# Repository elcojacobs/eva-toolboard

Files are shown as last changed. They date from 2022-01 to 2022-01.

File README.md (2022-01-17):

# Nema 14/17 Toolboard for EVA

Breakout board for EVA to mount to the back of a Nema 17 or name 17 motor. (31mm hole spacing or 43.8mm diagonally).

All signals and power are routed over 2 20p ribbon cables.
For the heater, 5 parallel wires are used to provide enough current. For part fan power, 2 parallel wires are used.

The same board is mounted at the hotend and near the main board.
On the main board side, most components are not mounted, only the connectors.
On the hotend side, all components are mounted except the terminal block in the middle.

## Features
- Everything wired through 2 ribbon cables.
- Spring terminal blocks for: heater, part fan, tool fan, probe, neopixel, aux 1-3
- ADXL345 on board
- Chamber temp PT1000 on board
- Neopixel LED on board and daisy chained to output terminal block
- 3 unused AUX signals

## Jumpers
- On the hotend side, connect 1 of the solder jumpers to select the voltage for the probe
- For correct neopixel routing, connect the hotend solder jumpers on the hotend side and the board solder jumpers on the main board side.

## License
Shield: [][cc-by-nc-sa]

This work is licensed under a
[Creative Commons Attribution-NonCommercial-ShareAlike 4.0 International License][cc-by-nc-sa].

[][cc-by-nc-sa]

[cc-by-nc-sa]: http://creativecommons.org/licenses/by-nc-sa/4.0/
[cc-by-nc-sa-image]: https://licensebuttons.net/l/by-nc-sa/4.0/88x31.png
[cc-by-nc-sa-shield]: https://img.shields.io/badge/License-CC%20BY--NC--SA%204.0-lightgrey.svg

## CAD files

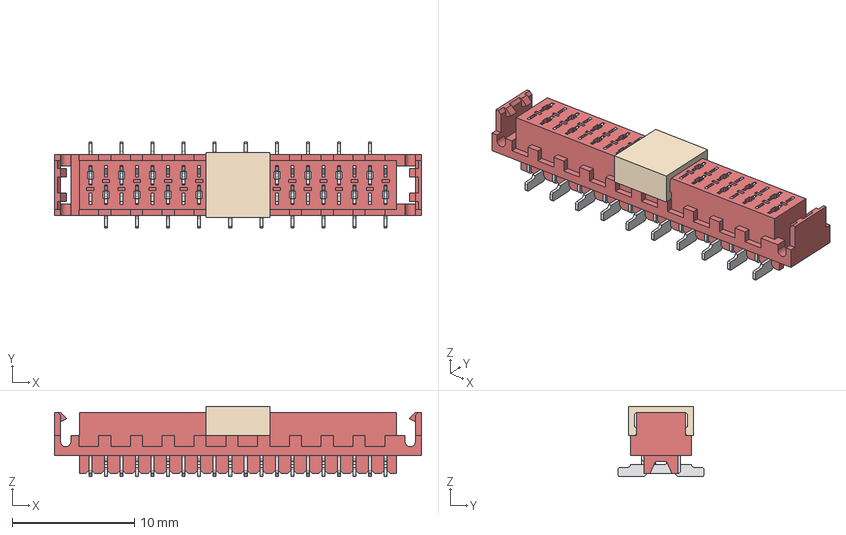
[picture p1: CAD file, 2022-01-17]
690367292076 (rev1).stp
30.0 x 7.00 x 5.75 mm
Gehäuse
Pick Pad
Pin x 20

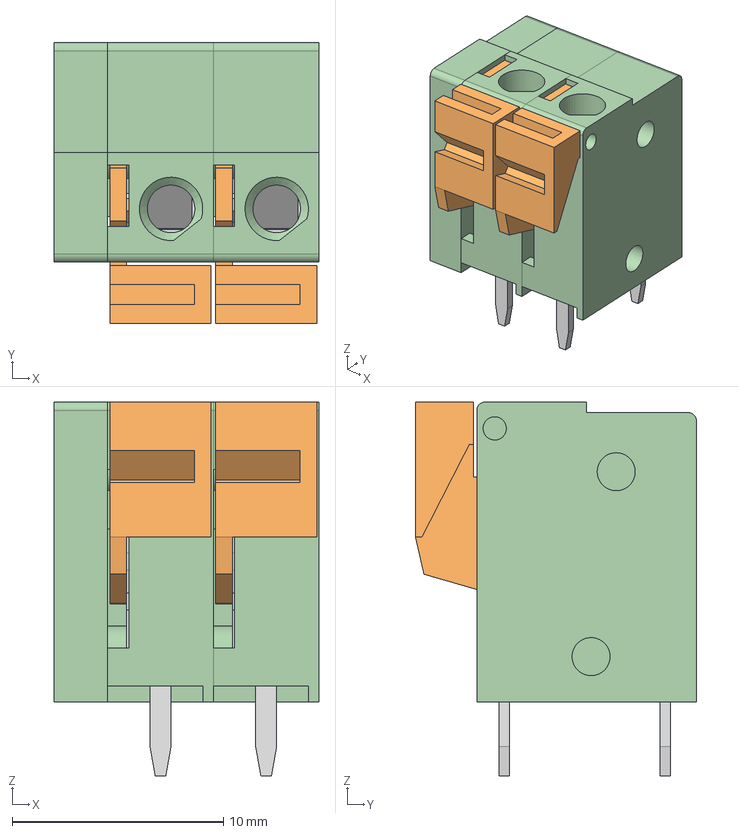
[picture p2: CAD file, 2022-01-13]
691401700002B (rev1).stp
12.5 x 13.3 x 17.7 mm
6914017000xx_CAPOT
6914017000xx x 4
6914017000xx_lame x 2
6914017000xx_Levier x 2

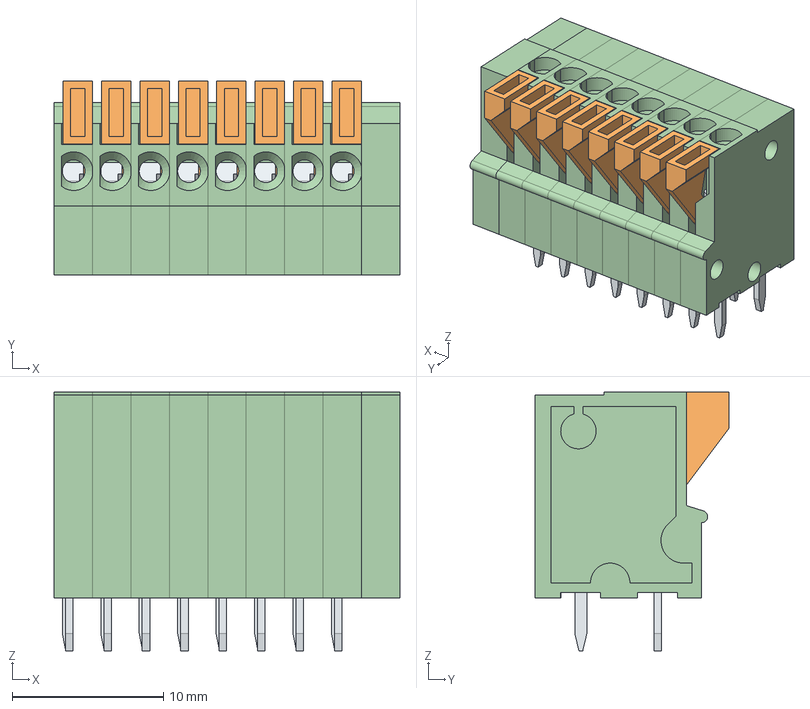
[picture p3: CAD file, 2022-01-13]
691403900008B (rev1).stp
22.9 x 12.8 x 17.1 mm
6914039000xx_CAPOT
6914039000xx x 8
6914039000xx_PIN x 8
6914039000xx_LEVIER x 8
6914039000xx_LAME x 8

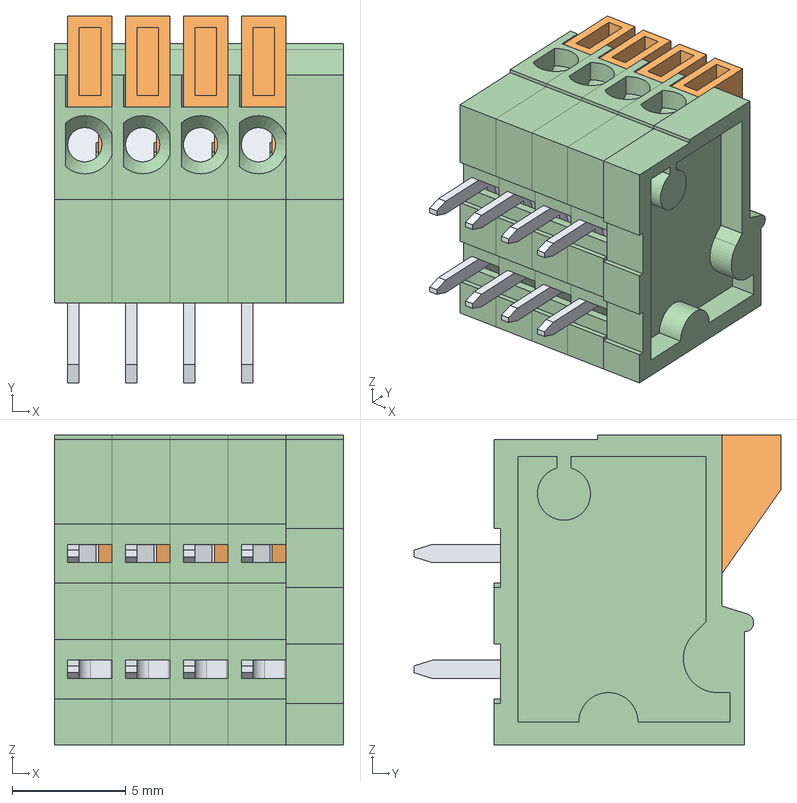
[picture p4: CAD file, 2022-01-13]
691402910004B (rev1).stp
12.7 x 16.1 x 13.6 mm
6914029100xx_CAPOT
6914029100xx x 4
6914029100xx_PIN x 4
6914029100xx_LAME x 4
6914029100xx_LEVIER x 4

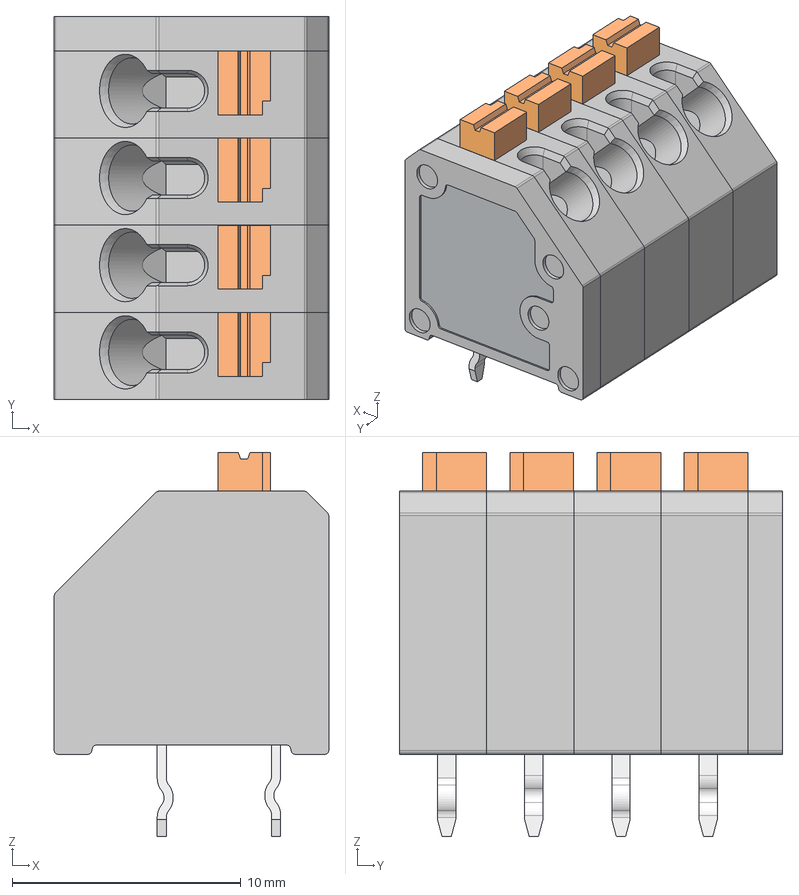
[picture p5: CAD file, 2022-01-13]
691412320004 (rev1).stp
12.0 x 16.7 x 16.8 mm
MRT24P3.81V01_SX1
MRT24P3.81V01_CNT5 x 2
MRT24P3.81V01_CNT4 x 2

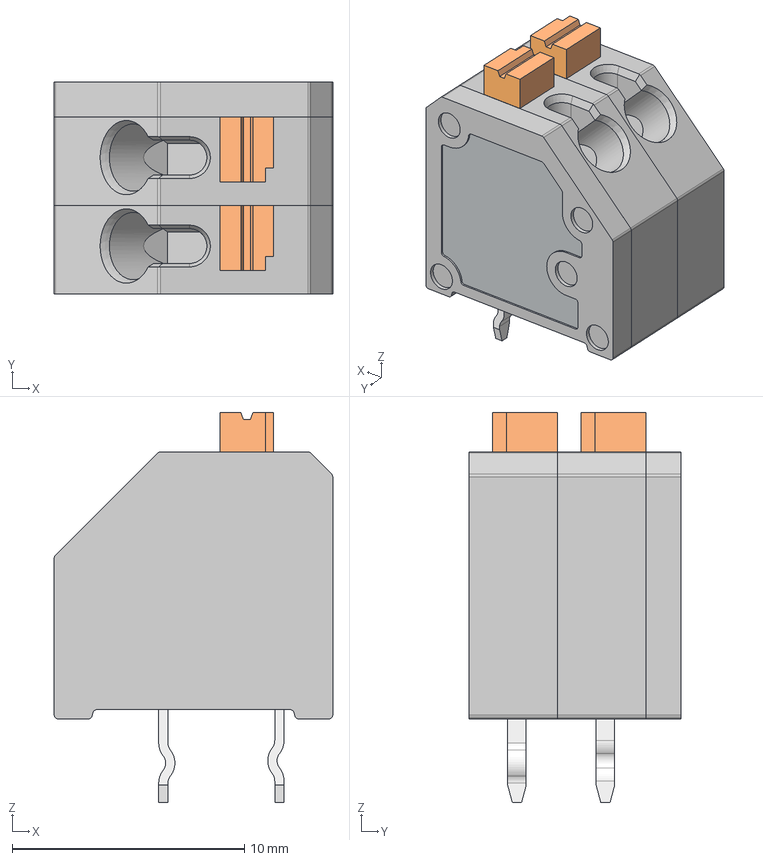
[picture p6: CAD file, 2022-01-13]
691412320002 (rev1).stp
12.0 x 9.12 x 16.8 mm
MRT24P3.81V01_SX1
MRT24P3.81V01_CNT5
MRT24P3.81V01_CNT4

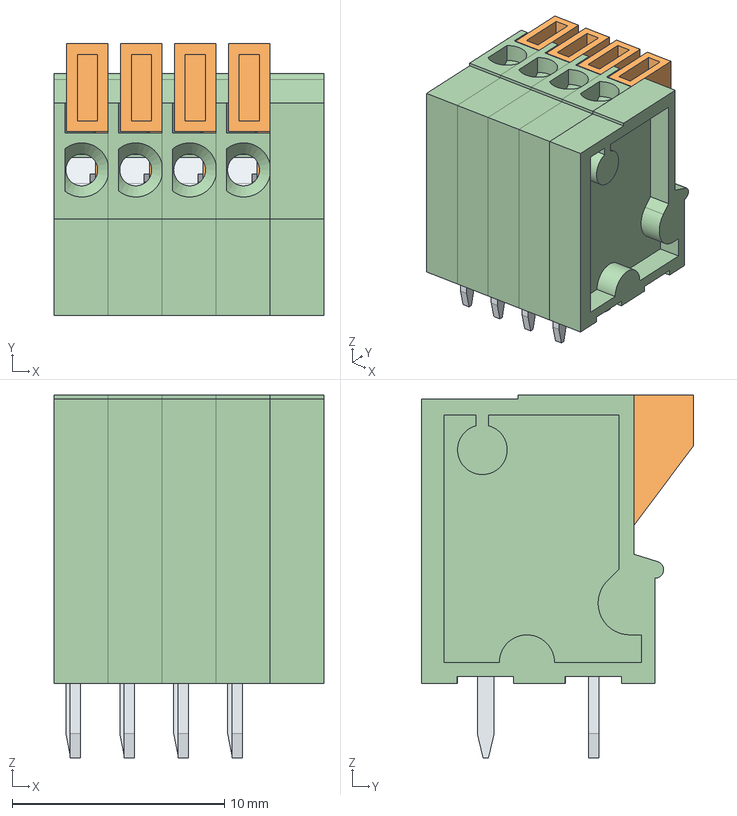
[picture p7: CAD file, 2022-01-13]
691403900004B (rev1).stp
12.7 x 12.8 x 17.1 mm
6914039000xx_CAPOT
6914039000xx x 4
6914039000xx_PIN x 4
6914039000xx_LEVIER x 4
6914039000xx_LAME x 4

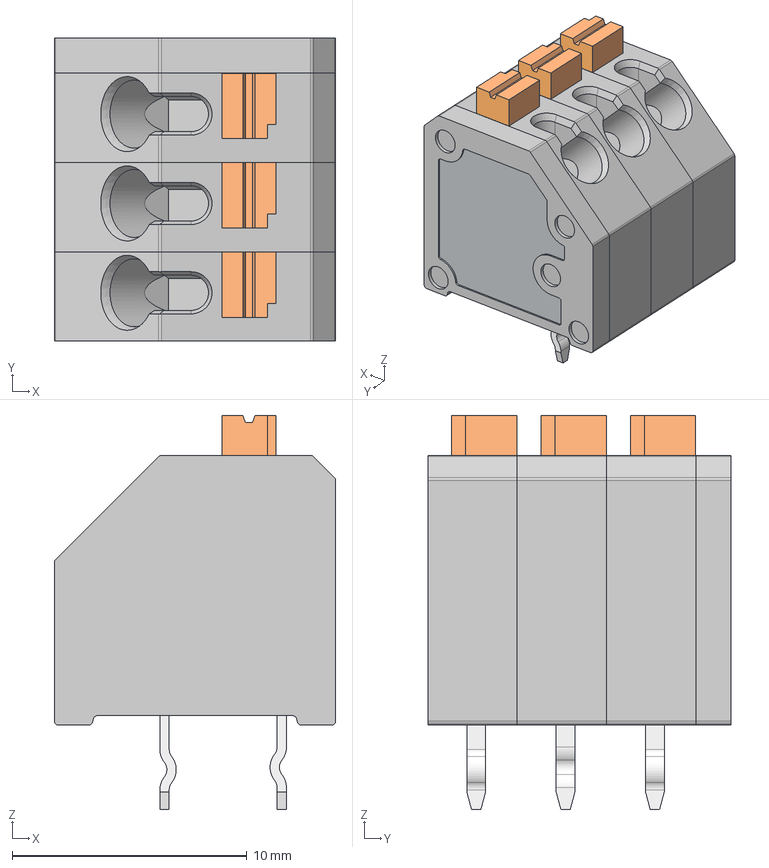
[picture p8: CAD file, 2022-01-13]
691412320003 (rev1).stp
12.0 x 12.9 x 16.8 mm
MRT24P3.81V01_SX1
MRT24P3.81V01_CNT5
MRT24P3.81V01_CNT4 x 2

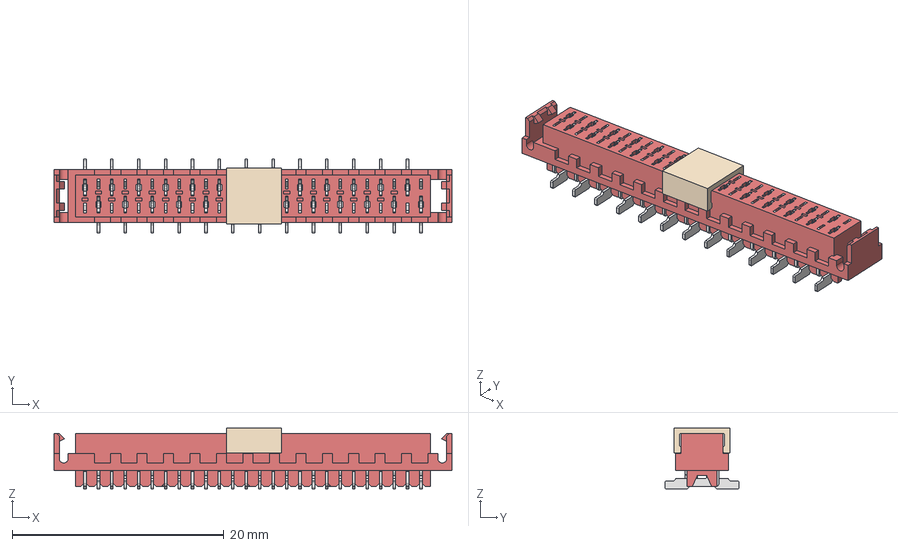
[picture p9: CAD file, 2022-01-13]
690367292676 (rev1).stp
37.6 x 7.00 x 5.75 mm
Gehäuse
Pick Pad
Pin x 26

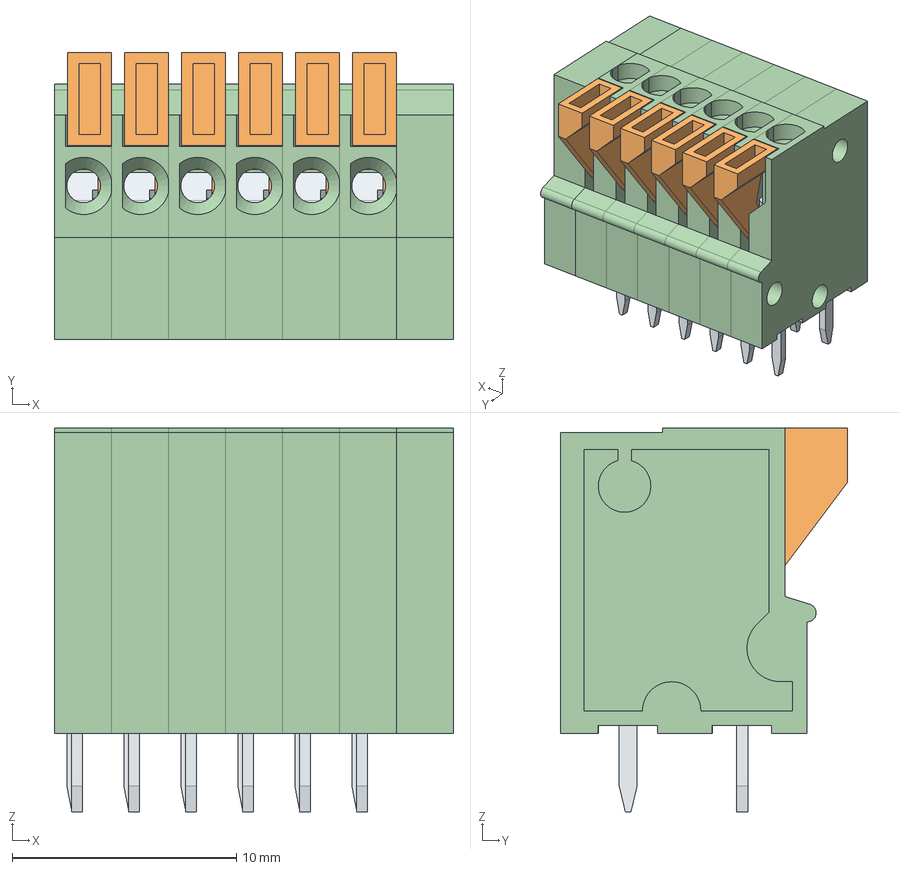
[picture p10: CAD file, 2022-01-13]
691403900006B (rev1).stp
17.8 x 12.8 x 17.1 mm
6914039000xx_CAPOT
6914039000xx x 6
6914039000xx_PIN x 6
6914039000xx_LEVIER x 6
6914039000xx_LAME x 6

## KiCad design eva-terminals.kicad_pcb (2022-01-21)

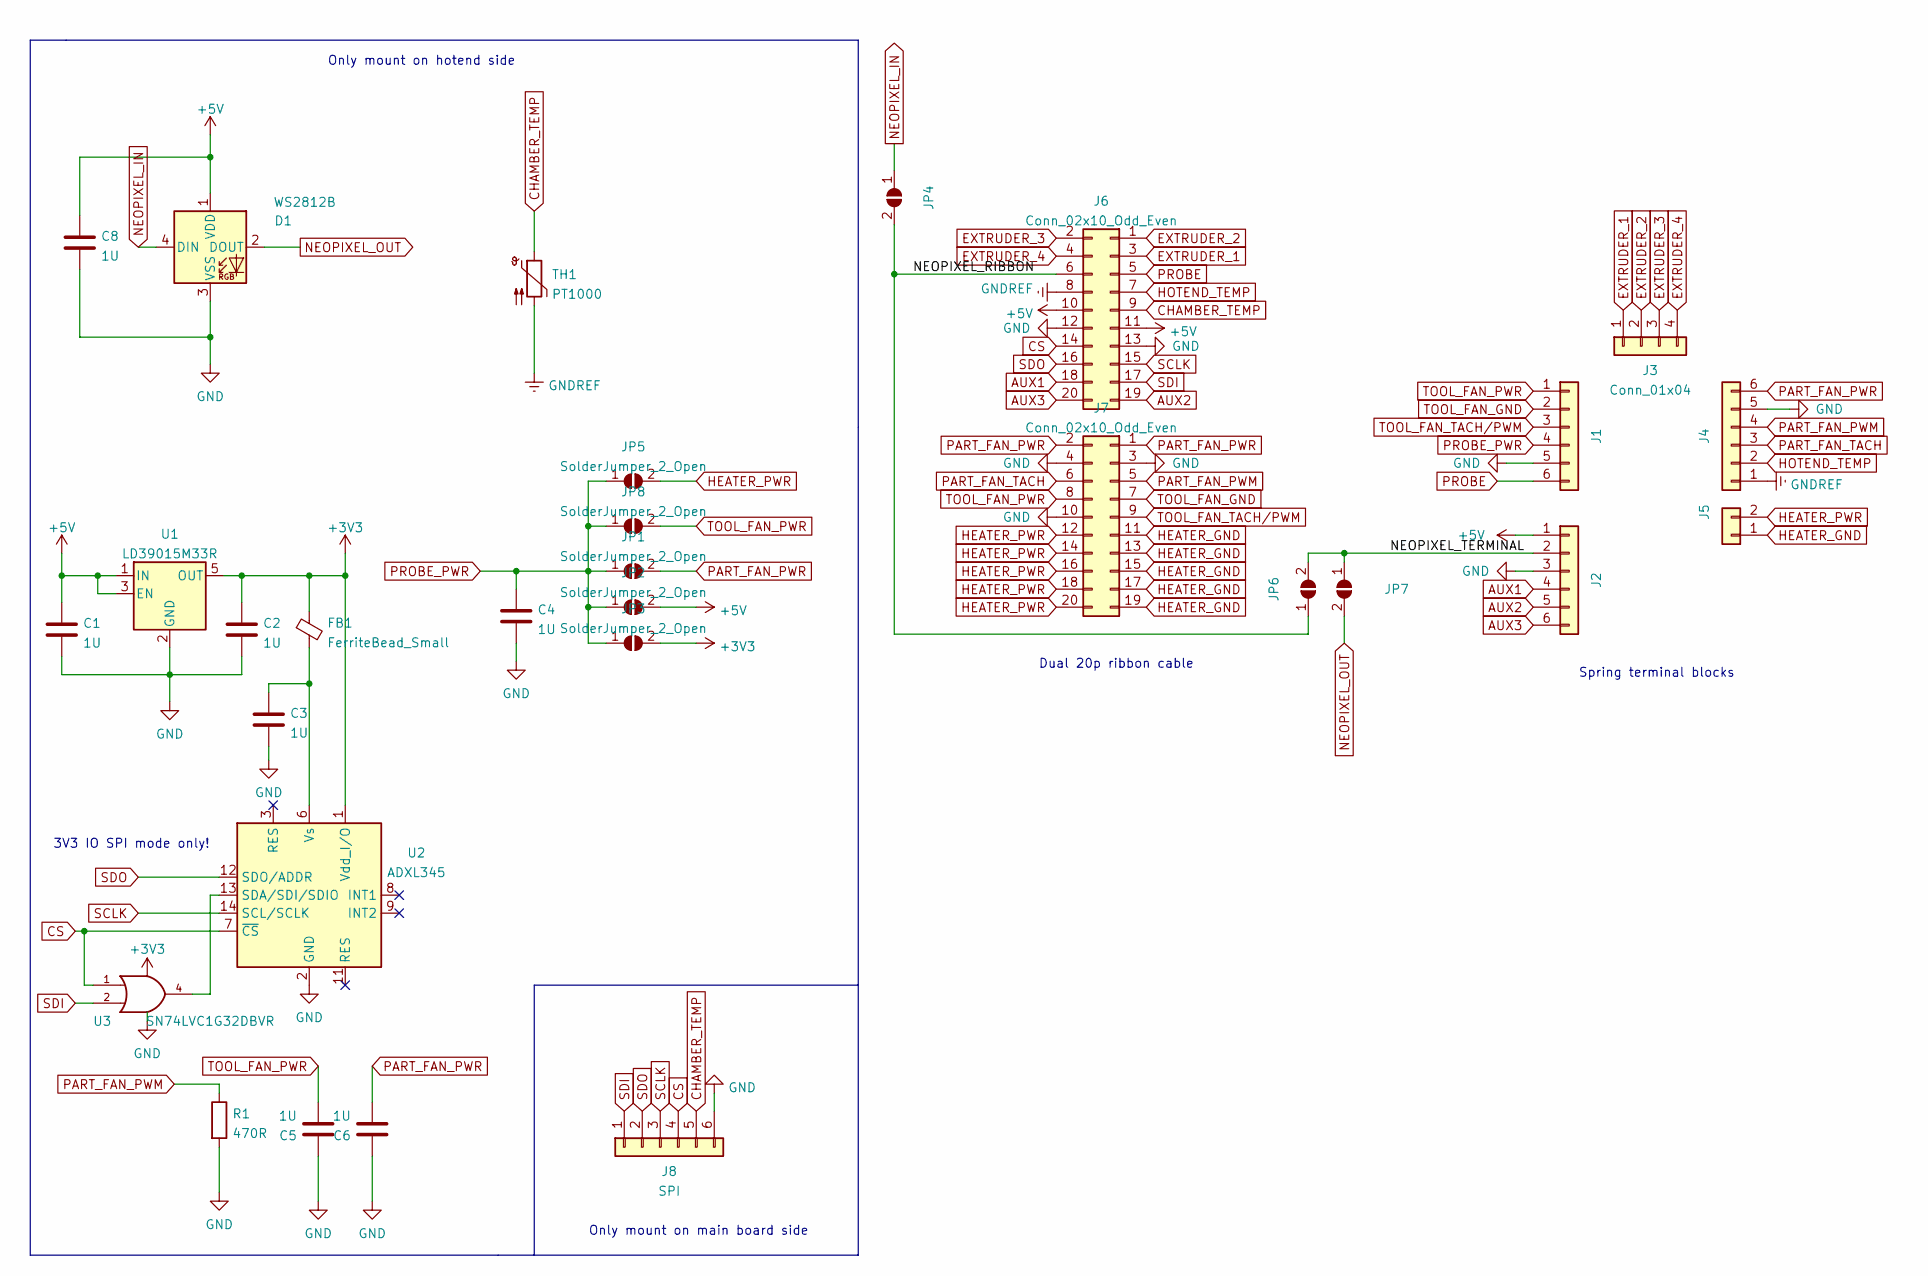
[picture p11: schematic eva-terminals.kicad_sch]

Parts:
C1, C2, C3, C4, C5, C6, C8: 1U; C_0805_2012Metric
D1: WS2812B; LED_WS2812B_PLCC4_5.0x5.0mm_P3.2mm
FB1: FerriteBead_Small; L_0603_1608Metric
J1, J2, J4: 691403900006B
J3: Conn_01x04; JST_XH_S4B-XH-A_1x04_P2.50mm_Horizontal
J5: HEATER; 691401700002B
J6, J7: Conn_02x10_Odd_Even; 690367292076
J8: SPI; 691403900006B
JP1, JP2, JP3, JP4, JP5, JP6, JP7, JP8: SolderJumper_2_Open; SolderJumper-2_P1.3mm_Open_RoundedPad1.0x1.5mm
R1: 470R; R_0603_1608Metric
TH1: PT1000; R_1206_3216Metric
U1: LD39015M33R; SOT-23-5
U2: ADXL345; LGA-14_3x5mm_P0.8mm_LayoutBorder1x6y
U3: SN74LVC1G32DBVR‎; SOT-23-5

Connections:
+3V3: C2.1, FB1.1, JP3.2 (B), U1.5 (OUT), U2.1 (Vdd_I/O), U3.5 (VCC)
+5V: C1.1, C8.1, D1.1 (VDD), J2.1, J2.A1 (Pin_1A), J6.10, J6.11, JP2.2 (B), U1.1 (IN), U1.3 (EN)
/NEOPIXEL_RIBBON: J6.6, JP4.2 (B), JP6.1 (A)
/NEOPIXEL_TERMINAL: J2.2, J2.A2, JP6.2 (B), JP7.1 (A)
AUX1: J2.4, J2.A4, J6.18
AUX2: J2.5, J2.A5, J6.19
AUX3: J2.6, J2.A6, J6.20
CHAMBER_TEMP: J6.9, J8.5, J8.A5, TH1.1
CS: J6.14, J8.4, J8.A4, U2.7 (~CS), U3.1
EXTRUDER_1: J3.1, J6.3
EXTRUDER_2: J3.2, J6.1
EXTRUDER_3: J3.3, J6.2
EXTRUDER_4: J3.4, J6.4
GND: C1.2, C2.2, C3.2, C4.2, C5.1, C6.1, C8.2, D1.3 (VSS), J1.5, J1.A5, J2.3, J2.A3 (Pin_3), J4.5, J4.A5, J6.12, J6.13, J7.3, J7.4, J7.10, J8.6, J8.A6, R1.2, U1.2 (GND), U2.2 (GND), U2.4 (GND), U2.5 (GND), U3.3 (GND)
GNDREF: J4.1, J4.A1 (Pin_1A), J6.8, TH1.2
HEATER_GND: J5.1, J5.A1 (Pin_1A), J7.11, J7.13, J7.15, J7.17, J7.19
HEATER_PWR: J5.2, J5.A2, J7.12, J7.14, J7.16, J7.18, J7.20, JP5.2 (B)
HOTEND_TEMP: J4.2, J4.A2, J6.7
NEOPIXEL_IN: D1.4 (DIN), JP4.1 (A)
NEOPIXEL_OUT: D1.2 (DOUT), JP7.2 (B)
unnamed: C3.1, FB1.2, U2.6 (Vs)
unnamed: U2.13 (SDA/SDI/SDIO), U3.4
PART_FAN_PWM: J4.4, J4.A4, J7.5, R1.1
PART_FAN_PWR: C6.2, J4.6, J4.A6, J7.1, J7.2, JP1.2 (B)
PART_FAN_TACH: J4.3, J4.A3 (Pin_3), J7.6
PROBE: J1.6, J1.A6, J6.5
PROBE_PWR: C4.1, J1.4, J1.A4, JP1.1 (A), JP2.1 (A), JP3.1 (A), JP5.1 (A), JP8.1 (A)
SCLK: J6.15, J8.3, J8.A3 (Pin_3), U2.14 (SCL/SCLK)
SDI: J6.17, J8.1, J8.A1 (Pin_1A), U3.2
SDO: J6.16, J8.2, J8.A2, U2.12 (SDO/ADDR)
TOOL_FAN_GND: J1.2, J1.A2, J7.7
TOOL_FAN_PWR: C5.2, J1.1, J1.A1 (Pin_1A), J7.8, JP8.2 (B)
TOOL_FAN_TACH/PWM: J1.3, J1.A3 (Pin_3), J7.9

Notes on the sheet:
Only mount on main board side
Only mount on hotend side
Spring terminal blocks
3V3 IO SPI mode only!
Dual 20p ribbon cable

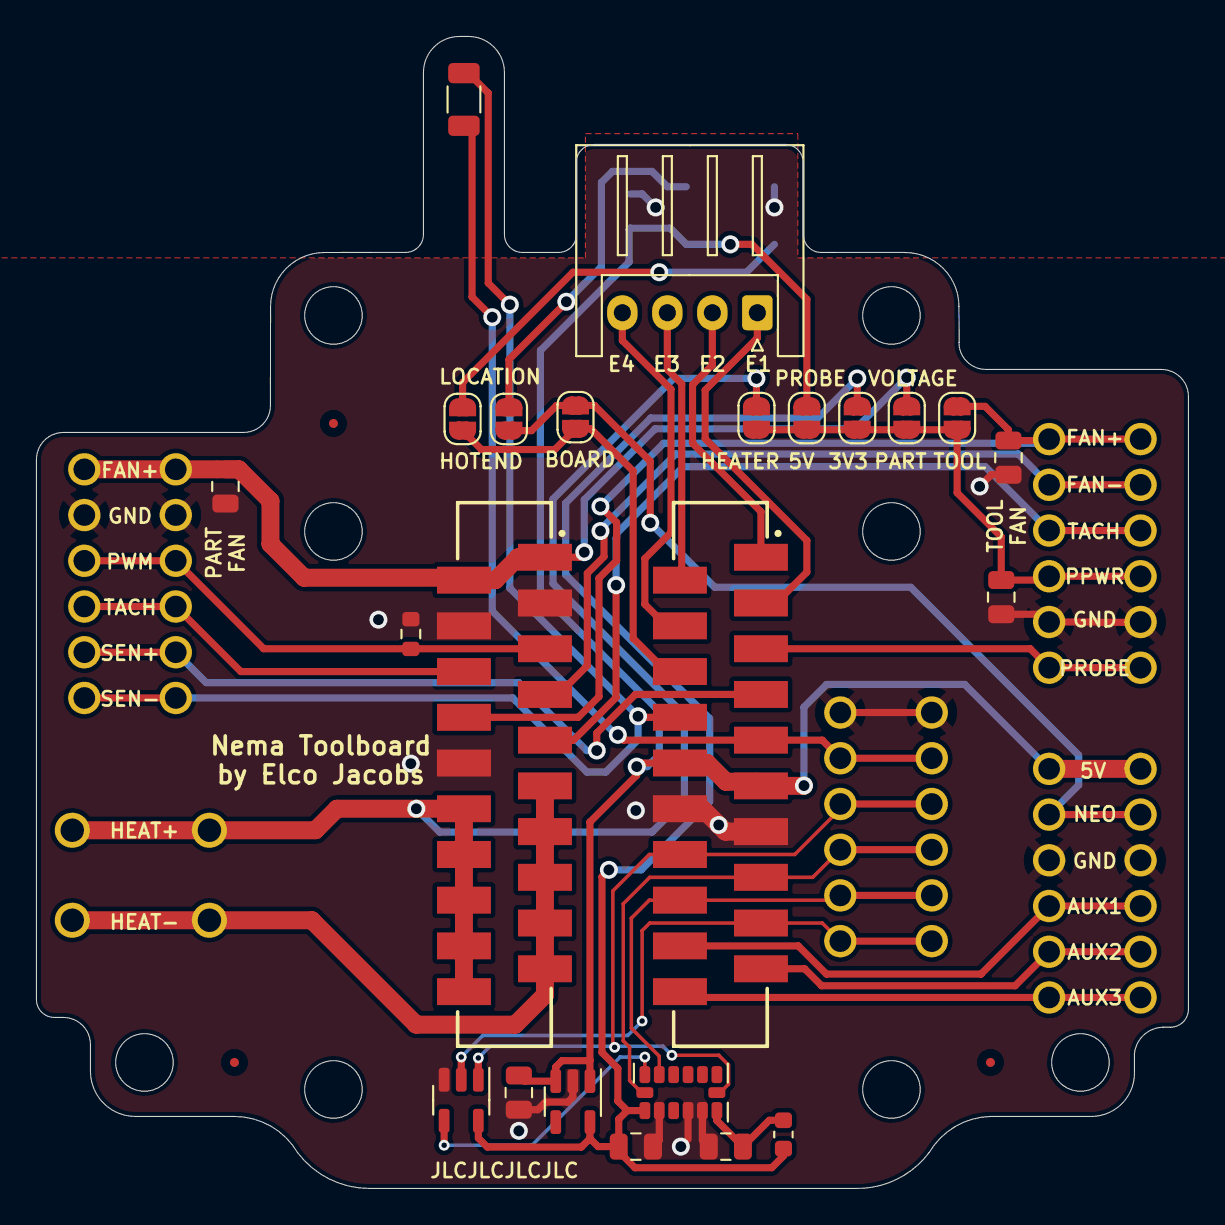
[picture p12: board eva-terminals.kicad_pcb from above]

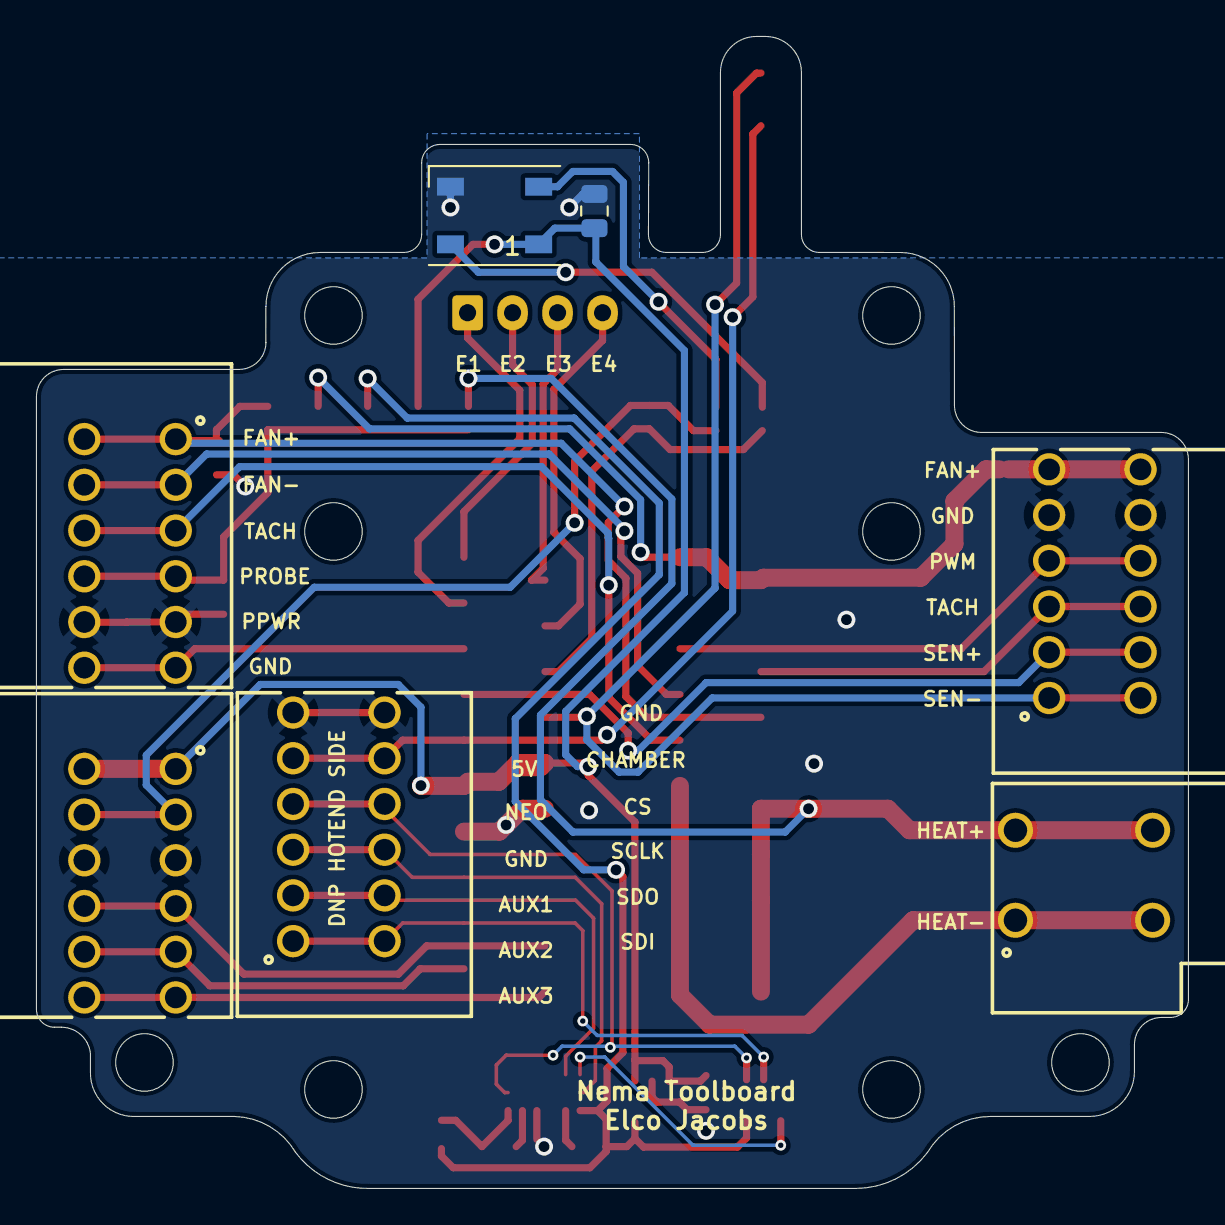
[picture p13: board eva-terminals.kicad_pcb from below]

Board: 2 copper layers, 64.0 x 64.0 mm, 30 parts (7 on the bottom side), 33 nets.

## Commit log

2022-01-13 initial commit wip
    [690367292676 (rev1).stp, 691401700002B (rev1).stp, 691402910004B (rev1).stp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]
2022-01-15 wip dual ribbon
    [eva-terminals.kicad_pcb, eva-terminals.kicad_sch]
2022-01-17 finalized board layout rev 1
    [690367292076 (rev1).stp, eva-terminals.kicad_pcb, eva-terminals.kicad_sch]
2022-01-17 more clearance for LGX bracket
    [eva-terminals.kicad_pcb]
2022-01-19 jst-xh for stepper
    [eva-terminals.kicad_pcb, eva-terminals.kicad_sch]
2022-01-19 change footprint for OR gate
    [eva-terminals.kicad_pcb, eva-terminals.kicad_sch]
2022-01-20 add heater voltage to selection for probe
    [eva-terminals.kicad_pcb]
2022-01-21 removed unncessary via in groundref
    [eva-terminals.kicad_pcb]
2022-01-21 add fiducial
    [eva-terminals.kicad_pcb]
2022-01-21 small changes
    [eva-terminals.kicad_pcb, eva-terminals.kicad_sch]
